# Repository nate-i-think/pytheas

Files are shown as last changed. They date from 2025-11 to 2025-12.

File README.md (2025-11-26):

# about pytheas
Pytheas is a custom ATSAMD21G18A-based (Cortex-M0+, arduino-compatible) flight controller which I have designed for a self-landing, thrust vectoring rocket which is being built by [Princeton Rocketry](https://www.princetonrocketry.com/) at Princeton University. Anyone is welcome to integrate it into their projects as long as they provide appropriate credit. However, no technical support is provided.

# features
 - ATSAMD21G18A microprocessor
   - Programmable via SWD (TagConnect, half-pitch DuPont) and USB
   - 10 exposed GPIO (plus 5 more extras in half-pitch)
   - Exposed I2C (recomended to connect GPS)
   - Everything else you'd expect
 - BMP390 Pressure Sensor
 - LSM6DSOXTR 6-Axis IMU
 - Power Regulation:
   - 5V @ 9A out (buck) with lots of capacitence  
   - 3v3 @ 1A out (LDO)
   - ~6–12V in

# renderings
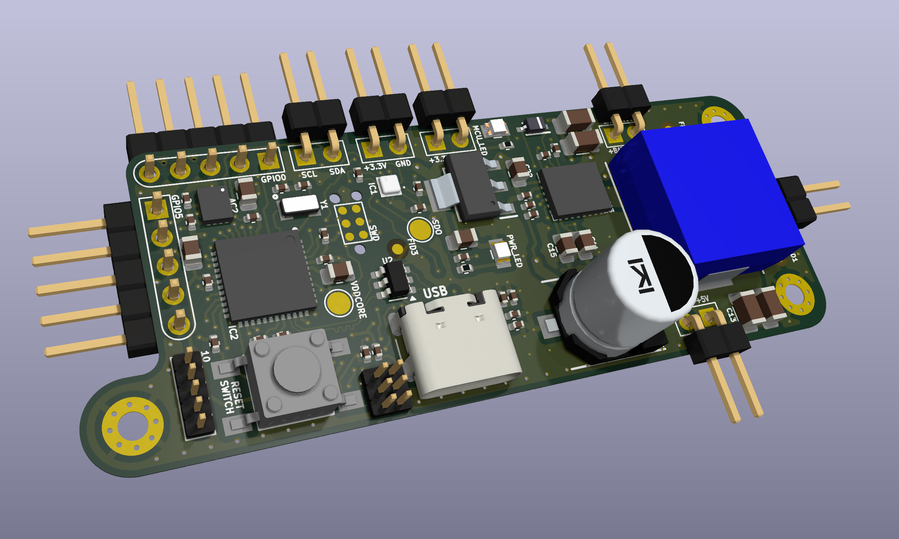
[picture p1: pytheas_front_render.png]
back_render

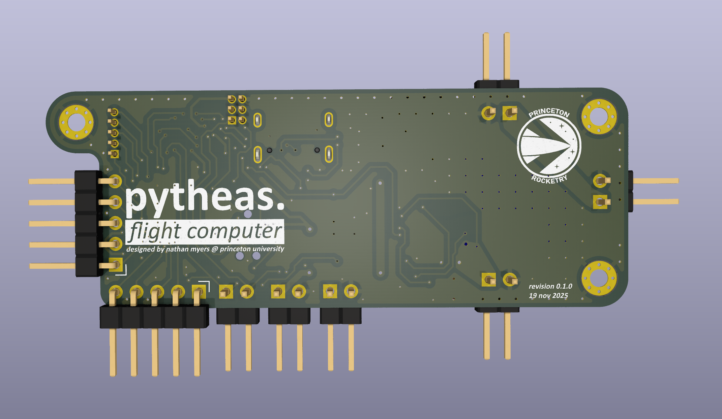
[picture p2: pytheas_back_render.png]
front_render


# layers
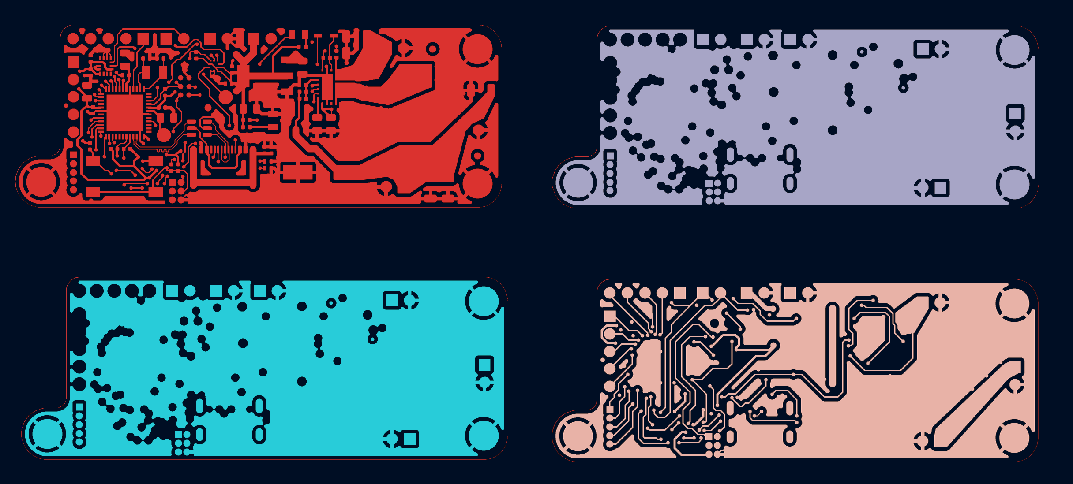
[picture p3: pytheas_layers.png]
layers image


# schematic
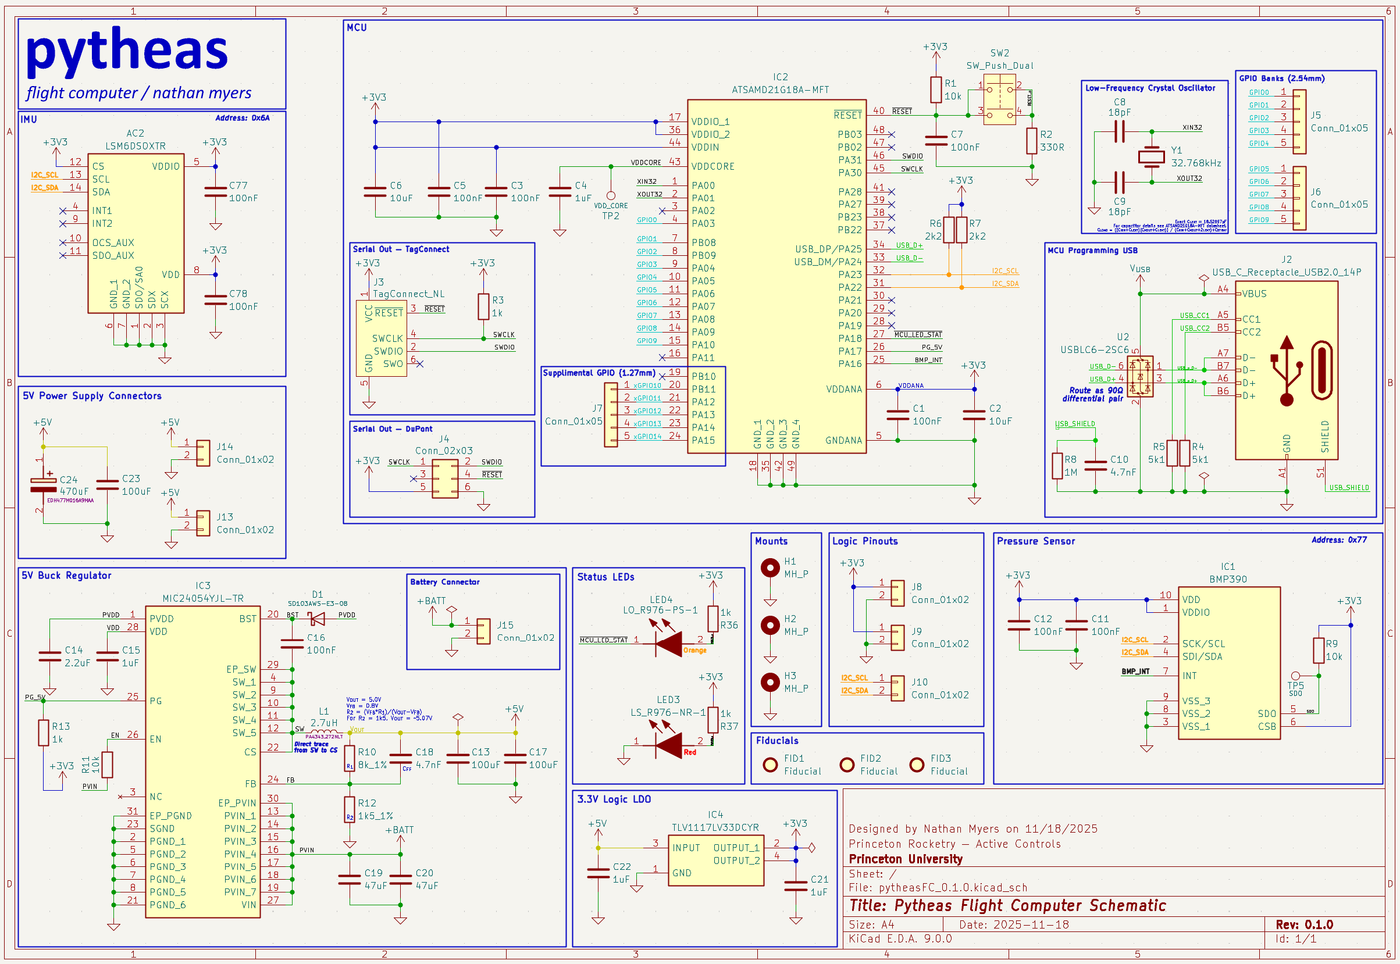
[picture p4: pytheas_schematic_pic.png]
schematic image


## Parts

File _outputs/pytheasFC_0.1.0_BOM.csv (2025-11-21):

Qty | Designator | Value | Footprint | Manufacturer | Manufacturer Part Number
1 | AC2 | LSM6DSOXTR | SamacSys_Parts:LGA-14_1 | STMicroelectronics | LSM6DSOXTR
9 | C1, C3, C5, C7, C11, C12, C16, C77, C78 | 100nF | Capacitor_SMD:C_0402_1005Metric
2 | C2, C6 | 10uF | Capacitor_SMD:C_0805_2012Metric
4 | C4, C15, C21, C22 | 1uF | Capacitor_SMD:C_0805_2012Metric
2 | C8, C9 | 18pF | Capacitor_SMD:C_0402_1005Metric
2 | C10, C18 | 4.7nF | Capacitor_SMD:C_0402_1005Metric
3 | C13, C17, C23 | 100uF | Capacitor_SMD:C_1206_3216Metric
1 | C14 | 2.2uF | Capacitor_SMD:C_0805_2012Metric
2 | C19, C20 | 47uF | Capacitor_SMD:C_1206_3216Metric
1 | C24 | 470uF | SamacSys_Parts:CAPAE830X1050N | KEMET | EDH477M016A9MAA
1 | D1 | SD103AWS-E3-08 | SamacSys_Parts:SOD2713X115N | Vishay Semiconductors | SD103AWS-E3-08
1 | IC1 | BMP390 | SamacSys_Parts:BMP390 | BOSCH | BMP390
1 | IC2 | ATSAMD21G18A-MFT | SamacSys_Parts:QFN50P700X700X90-49N-D | Microchip | ATSAMD21G18A-MFT
1 | IC3 | MIC24054YJL-TR | SamacSys_Parts:MIC24054YJLTR | Microchip | MIC24054YJL-TR
1 | IC4 | TLV1117LV33DCYR | SamacSys_Parts:SOT230P700X180-4N | Texas Instruments | TLV1117LV33DCYR
1 | J2 | USB_C_Receptacle_USB2.0_14P | Connector_USB:USB_C_Receptacle_GCT_USB4105-xx-A_16P_TopMnt_Horizontal | GCT | USB4105-GF-A
1 | L1 | 2.7uH | SamacSys_Parts:INDPM140128X650N | PULSE | PA4343.272NLT
1 | LED3 | LS_R976-NR-1 | SamacSys_Parts:LEDC2012X40N | ams OSRAM | LS R976-NR-1
1 | LED4 | LO_R976-PS-1 | SamacSys_Parts:LEDC2012X90N | ams OSRAM | LO R976-PS-1
3 | R1, R9, R11 | 10k | Capacitor_SMD:C_0402_1005Metric
1 | R2 | 330R | Capacitor_SMD:C_0402_1005Metric
2 | R3, R13 | 1k | Capacitor_SMD:C_0402_1005Metric
2 | R4, R5 | 5k1 | Capacitor_SMD:C_0402_1005Metric
2 | R6, R7 | 2k2 | Capacitor_SMD:C_0402_1005Metric
1 | R8 | 1M | Capacitor_SMD:C_0402_1005Metric
1 | R10 | 8k_1% | Capacitor_SMD:C_0402_1005Metric
1 | R12 | 1k5_1% | Capacitor_SMD:C_0402_1005Metric
2 | R36, R37 | 1k | Resistor_SMD:R_0402_1005Metric
1 | SW2 | SW_Push_Dual | SamacSys_Parts:FSM2J_1 | TE Connectivity / P&B | 2-1437565-8
1 | U2 | USBLC6-2SC6 | Package_TO_SOT_SMD:SOT-23-6 | STMicroelectronics | USBLC6-2SC6
1 | Y1 | 32.768kHz | SamacSys_Parts:ECX-31B | ECS | ECS-.327-12.5-34B-TR

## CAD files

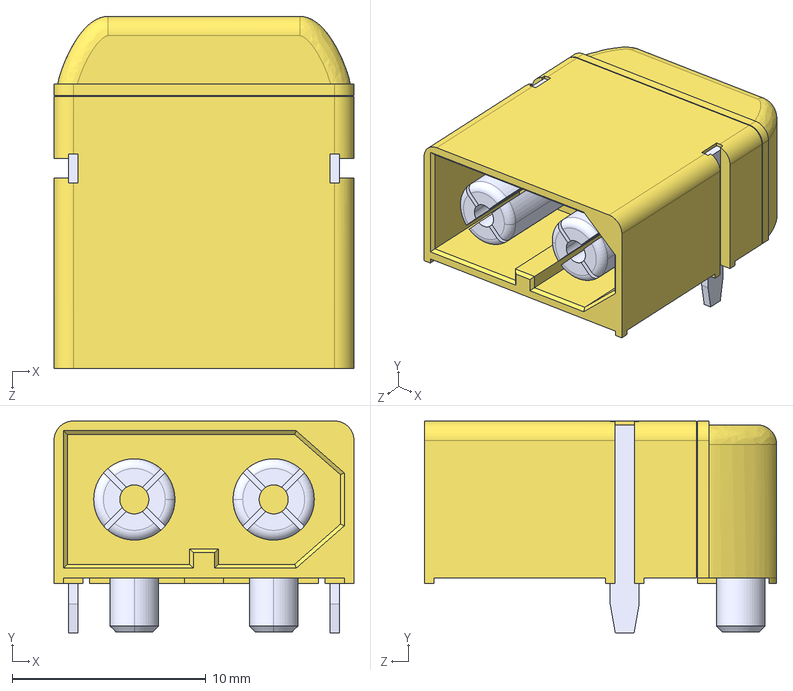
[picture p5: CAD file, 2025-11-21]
Footprints/XT60PW-M/XT60PW-M.step
15.5 x 10.9 x 18.2 mm

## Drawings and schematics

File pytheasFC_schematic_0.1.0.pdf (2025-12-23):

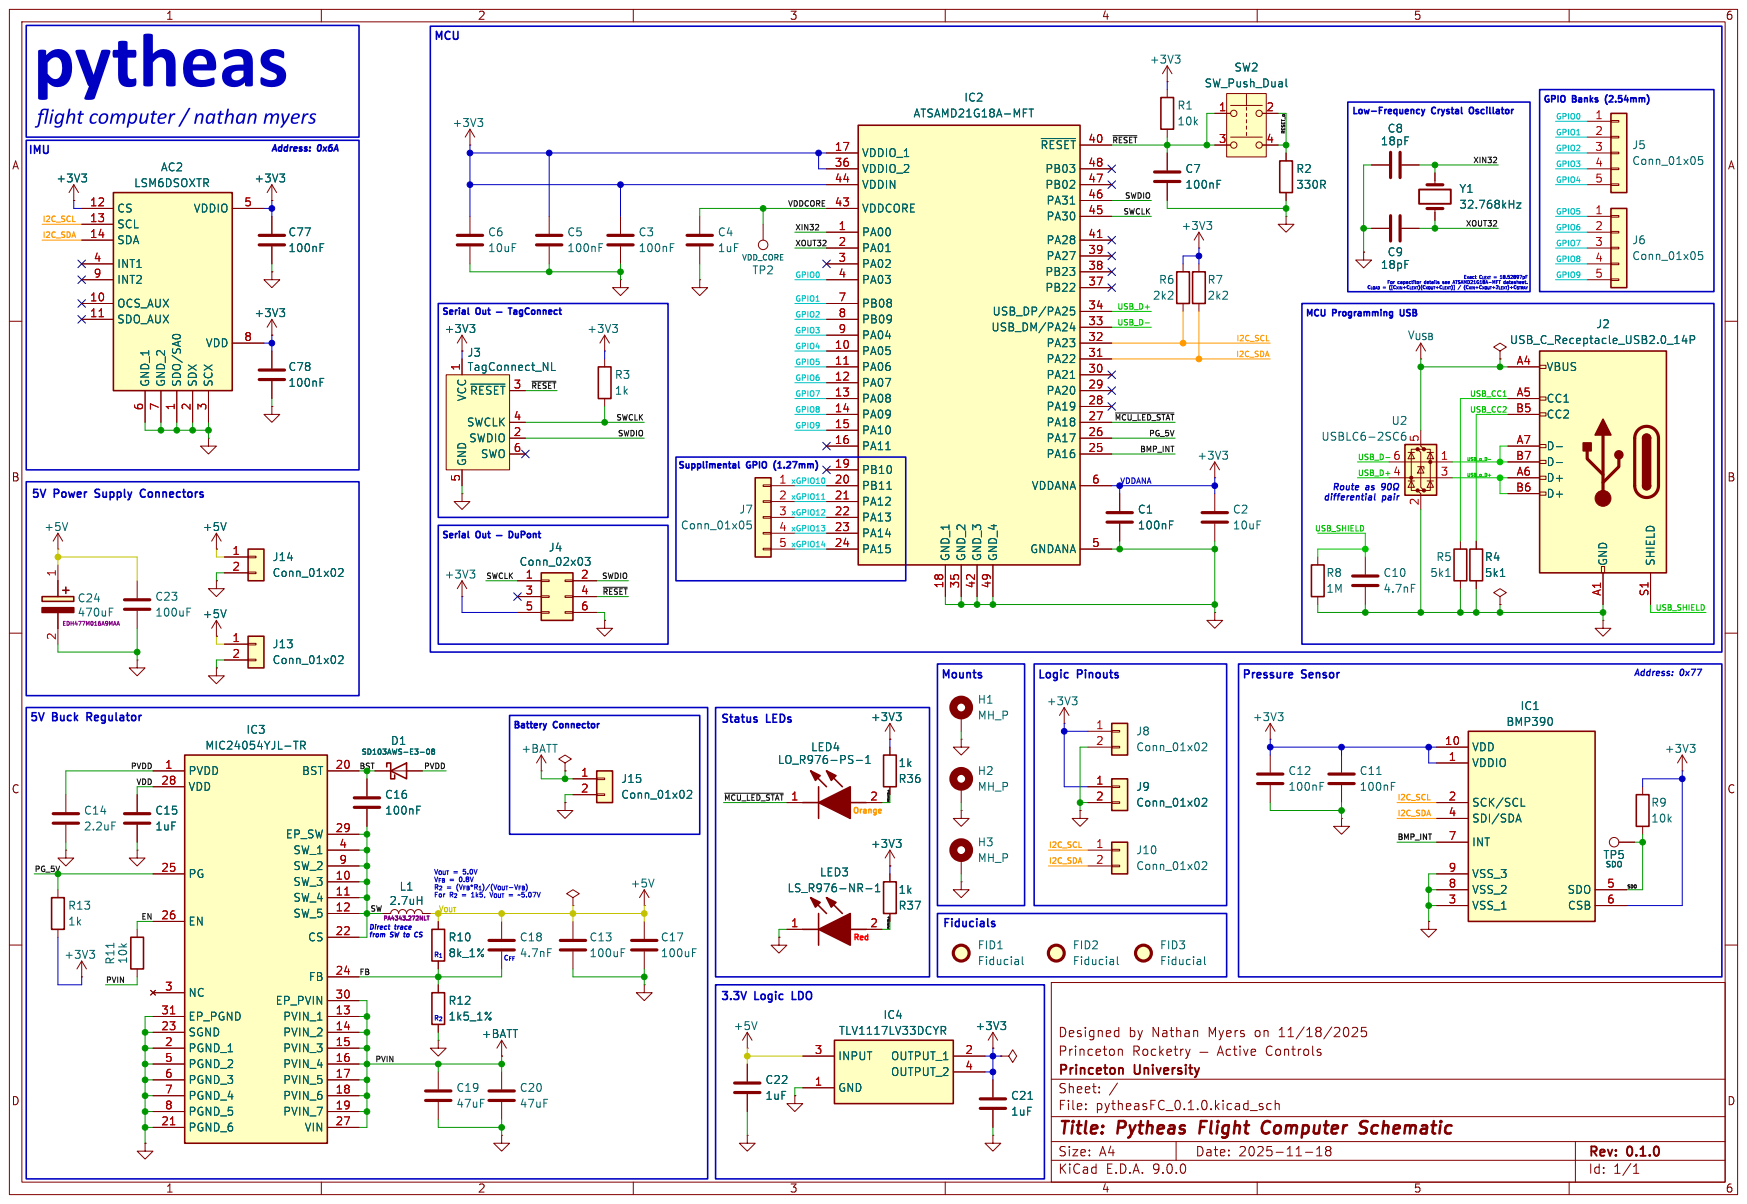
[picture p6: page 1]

5 ~{RESET}3 SWCLK 4 SWDIO 2 SWO 6

Id: 1/1 Title: Pytheas Flight Computer Schematic

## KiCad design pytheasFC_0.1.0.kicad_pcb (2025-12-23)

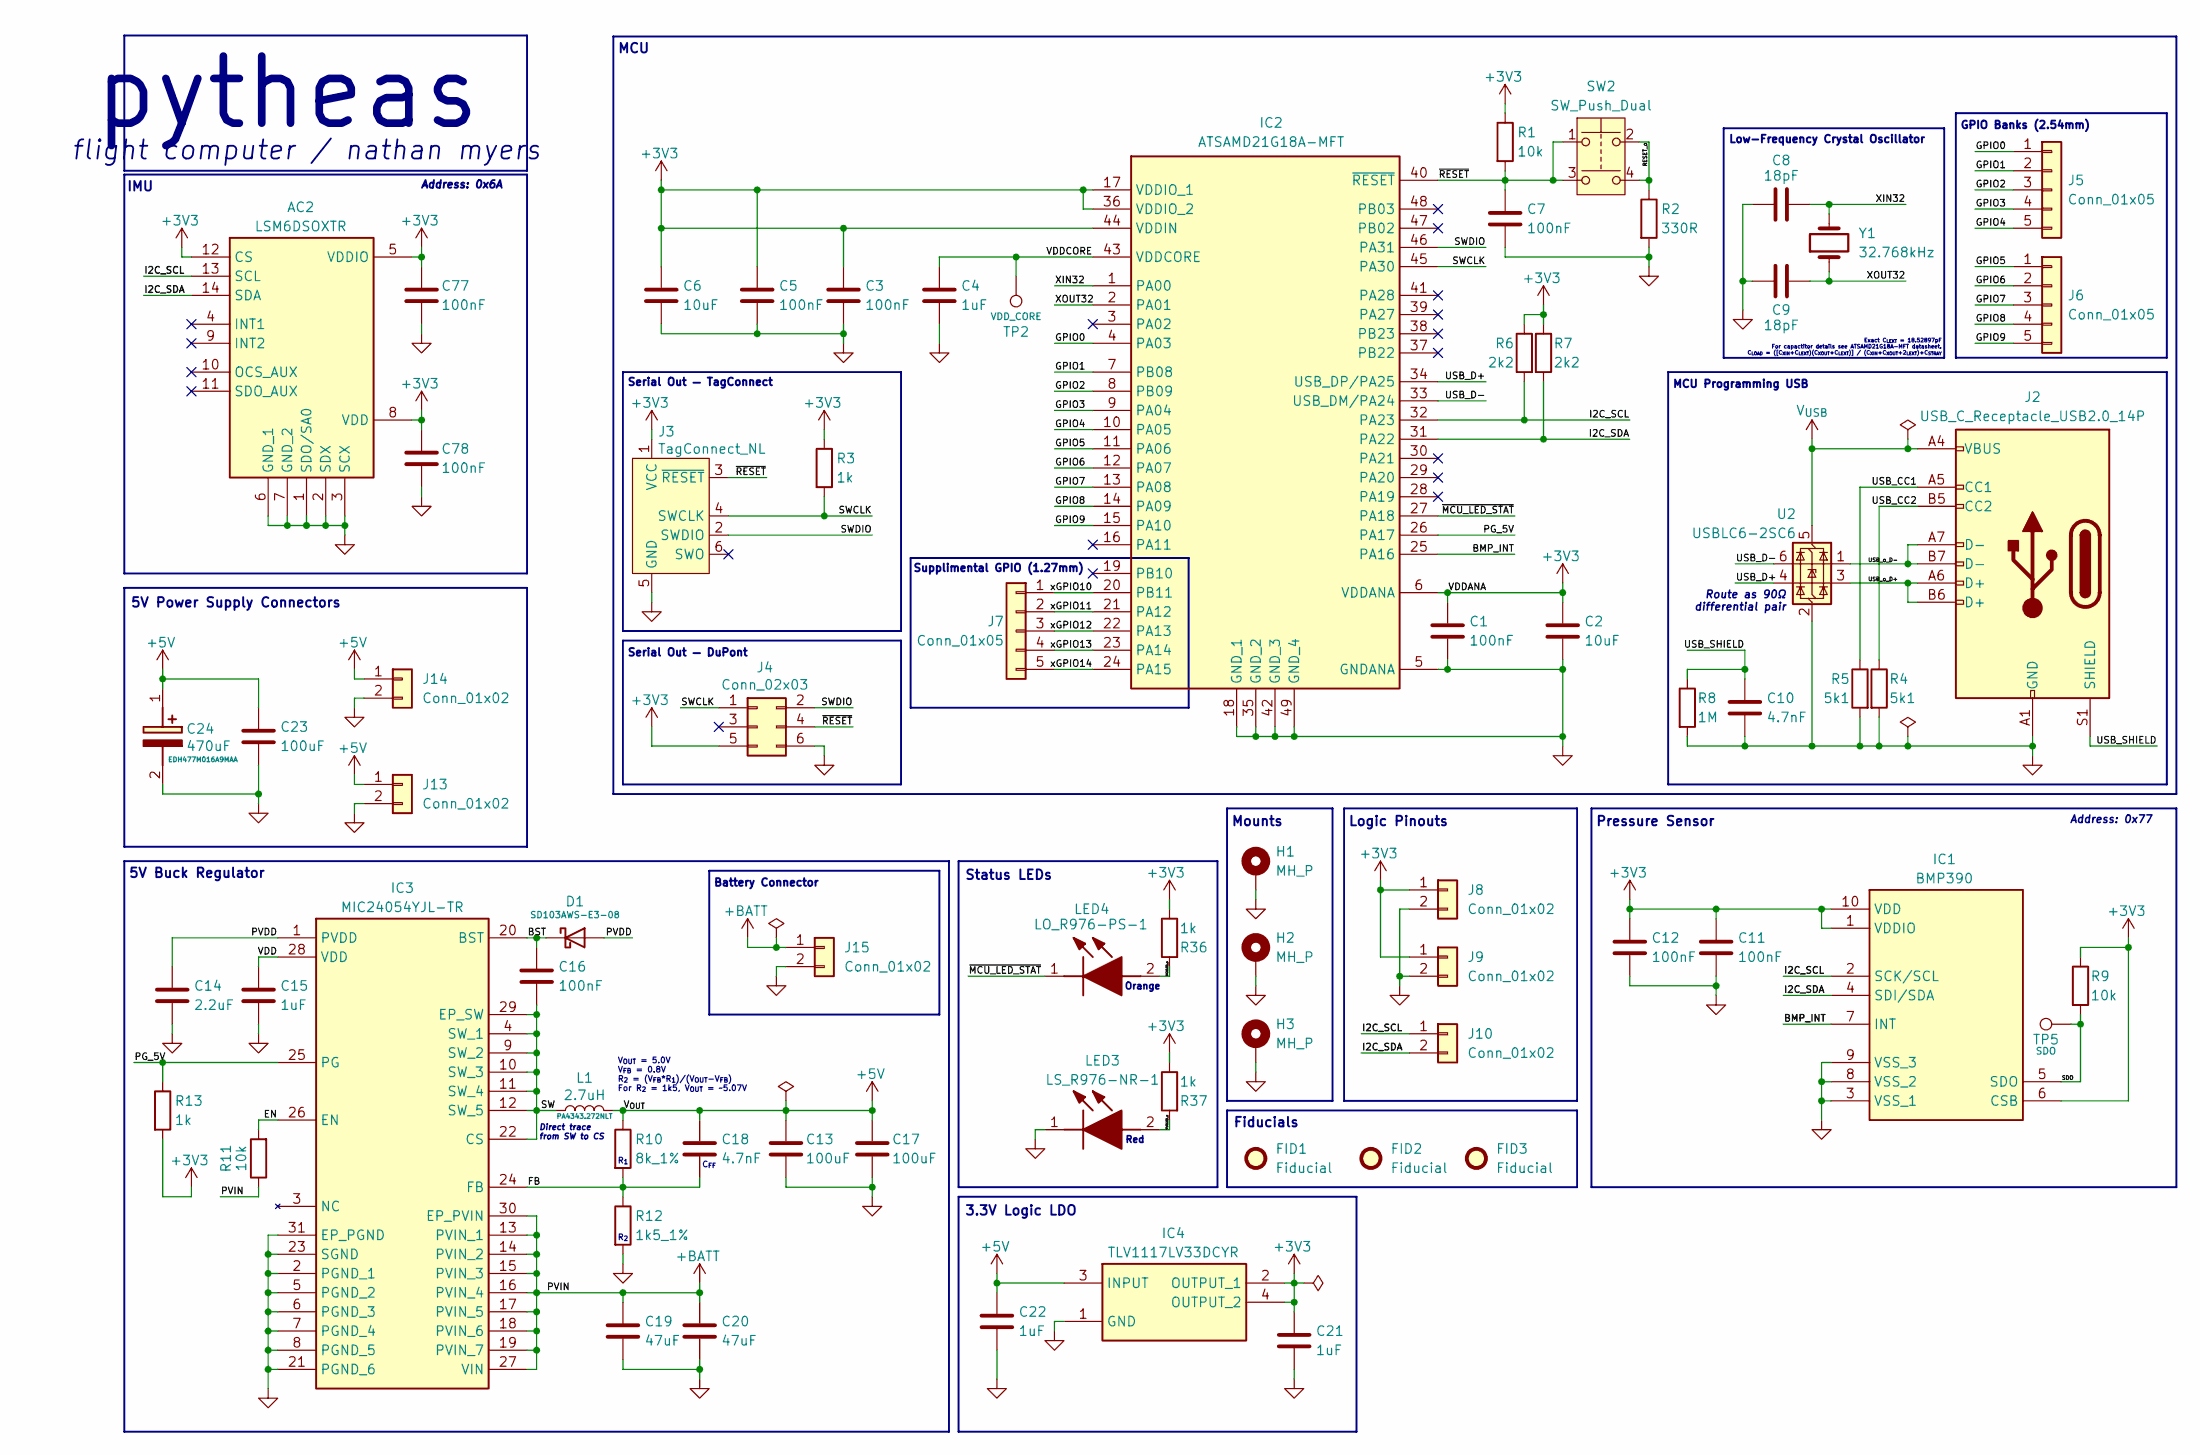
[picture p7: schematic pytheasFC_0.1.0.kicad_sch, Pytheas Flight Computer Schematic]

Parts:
AC2: LSM6DSOXTR; LGA-14_1; Mouser Part Number 511-LSM6DSOXTR
C1, C3, C5, C7, C11, C12, C16, C77, C78: 100nF; C_0402_1005Metric
C2, C6: 10uF; C_0805_2012Metric
C4, C15, C21, C22: 1uF; C_0805_2012Metric
C8, C9: 18pF; C_0402_1005Metric
C10, C18: 4.7nF; C_0402_1005Metric
C13, C17, C23: 100uF; C_1206_3216Metric
C14: 2.2uF; C_0805_2012Metric
C19, C20: 47uF; C_1206_3216Metric
C24: 470uF; CAPAE830X1050N; Mouser Part Number 80-EDH477M016A9MAA
D1: SD103AWS-E3-08; SOD2713X115N; Part Number SD103AWS-E3-08
FID1, FID2, FID3: Fiducial; Fiducial_1mm_Mask2mm
H1, H2, H3: MH_P; MountingHole_2.2mm_M2_Pad_Via
IC1: BMP390; Mouser Part Number 262-BMP390
IC2: ATSAMD21G18A-MFT; QFN50P700X700X90-49N-D; Mouser Part Number 556-ATSAMD21G18A-MFT
IC3: MIC24054YJL-TR; MIC24054YJLTR; Mouser Part Number 998-MIC24054YJLTR
IC4: TLV1117LV33DCYR; SOT230P700X180-4N; Mouser Part Number 595-TLV1117LV33DCYR
J2: USB_C_Receptacle_USB2.0_14P; USB_C_Receptacle_GCT_USB4105-xx-A_16P_TopMnt_Horizontal
J3: TagConnect_NL; Tag-Connect_TC2030-IDC-NL_2x03_P1.27mm_Vertical
J4: Conn_02x03; PinHeader_2x03_P1.27mm_Vertical
J5, J6: Conn_01x05; PinHeader_1x05_P2.54mm_Horizontal
J7: Conn_01x05; PinHeader_1x05_P1.27mm_Vertical
J8, J9, J10, J13, J14, J15: Conn_01x02; PinHeader_1x02_P2.54mm_Horizontal
L1: 2.7uH; INDPM140128X650N; Part Number PA4343.272NLT
LED3: LS_R976-NR-1; LEDC2012X40N; Mouser Part Number 720-LSR976-NR-1
LED4: LO_R976-PS-1; LEDC2012X90N; Mouser Part Number 720-LOR976-PS-1
R1, R9, R11: 10k; R_0402_1005Metric
R2: 330R; R_0402_1005Metric
R3, R13, R36, R37: 1k; R_0402_1005Metric
R4, R5: 5k1; R_0402_1005Metric
R6, R7: 2k2; R_0402_1005Metric
R8: 1M; R_0402_1005Metric
R10: 8k_1%; R_0402_1005Metric
R12: 1k5_1%; R_0402_1005Metric
SW2: SW_Push_Dual; FSM2J_1; Part Number 2-1437565-8
TP2: VDD_CORE; TestPoint_Pad_D2.0mm
TP5: SDO; TestPoint_Pad_D2.0mm
U2: USBLC6-2SC6; SOT-23-6
Y1: 32.768kHz; ECX-31B; Part Number ECS-.327-12.5-34B-TR

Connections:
+3V3: AC2.5 (VDDIO), AC2.8 (VDD), AC2.12 (CS), C1.1, C2.1, C3.1, C5.1, C6.1, C11.1, C12.1, C21.1, C77.1, C78.1, IC1.1 (VDDIO), IC1.6 (CSB), IC1.10 (VDD), IC2.6 (VDDANA), IC2.17 (VDDIO_1), IC2.36 (VDDIO_2), IC2.44 (VDDIN), IC4.2 (OUTPUT_1), IC4.4 (OUTPUT_2), J3.1 (VCC), J4.5, J8.1, J9.1, R1.1, R3.1, R6.1, R7.1, R9.1, R13.2, R36.1, R37.1
+5V: C13.1, C17.1, C18.1, C22.1, C23.1, C24.1 (+), IC4.3 (INPUT), J13.1, J14.1, L1.2, R10.1
+BATT: C19.1, C20.1, IC3.13 (PVIN_1), IC3.14 (PVIN_2), IC3.15 (PVIN_3), IC3.16 (PVIN_4), IC3.17 (PVIN_5), IC3.18 (PVIN_6), IC3.19 (PVIN_7), IC3.27 (VIN), IC3.30 (EP_PVIN), J15.1, R11.1
/BMP_INT: IC1.7 (INT), IC2.25 (PA16)
/BST: C16.1, D1.1 (K), IC3.20 (BST)
/EN: IC3.26 (EN), R11.2
/FB: C18.2, IC3.24 (FB), R10.2, R12.1
/GPIO0: IC2.4 (PA03), J5.1
/GPIO1: IC2.7 (PB08), J5.2
/GPIO2: IC2.8 (PB09), J5.3
/GPIO3: IC2.9 (PA04), J5.4
/GPIO4: IC2.10 (PA05), J5.5
/GPIO5: IC2.11 (PA06), J6.1
/GPIO6: IC2.12 (PA07), J6.2
/GPIO7: IC2.13 (PA08), J6.3
/GPIO8: IC2.14 (PA09), J6.4
/GPIO9: IC2.15 (PA10), J6.5
/I2C_SCL: AC2.13 (SCL), IC1.2 (SCK/SCL), IC2.32 (PA23), J10.1, R6.2
/I2C_SDA: AC2.14 (SDA), IC1.4 (SDI/SDA), IC2.31 (PA22), J10.2, R7.2
/MCULED_o: LED4.2 (A), R36.2
/PG_5V: IC2.26 (PA17), IC3.25 (PG), R13.1
/PVDD: C14.1, D1.2 (A), IC3.1 (PVDD)
/PWRLED_o: LED3.2 (A), R37.2
/RESET_o: R2.1, SW2.2, SW2.4
/SDO: IC1.5 (SDO), R9.2, TP5.1
/SW: C16.2, IC3.4 (SW_1), IC3.9 (SW_2), IC3.10 (SW_3), IC3.11 (SW_4), IC3.12 (SW_5), IC3.22 (CS), IC3.29 (EP_SW), L1.1
/SWCLK: IC2.45 (PA30), J3.4 (SWCLK), J4.1, R3.2
/SWDIO: IC2.46 (PA31), J3.2 (SWDIO), J4.2
/USB_CC1: J2.A5 (CC1), R5.1
/USB_CC2: J2.B5 (CC2), R4.1
/USB_D+: IC2.34 (USB_DP/PA25), U2.4 (I/O2)
/USB_D-: IC2.33 (USB_DM/PA24), U2.6 (I/O1)
/USB_SHIELD: C10.1, J2.S1 (SHIELD), R8.1
/USB_o_D+: J2.A6 (D+), J2.B6 (D+), U2.3 (I/O2)
/USB_o_D-: J2.A7 (D-), J2.B7 (D-), U2.1 (I/O1)
/VDD: C15.1, IC3.28 (VDD)
/VDDCORE: C4.1, IC2.43 (VDDCORE), TP2.1
/XIN32: C8.2, IC2.1 (PA00), Y1.2
/XOUT32: C9.1, IC2.2 (PA01), Y1.1
/xGPIO10: IC2.20 (PB11), J7.1
/xGPIO11: IC2.21 (PA12), J7.2
/xGPIO12: IC2.22 (PA13), J7.3
/xGPIO13: IC2.23 (PA14), J7.4
/xGPIO14: IC2.24 (PA15), J7.5
/~MCU_LED_STAT: IC2.27 (PA18), LED4.1 (K)
/~RESET: C7.1, IC2.40 (~RESET), J3.3 (~RESET), J4.4, R1.2, SW2.1, SW2.3
GND: AC2.1 (SDO/SA0), AC2.2 (SDX), AC2.3 (SCX), AC2.6 (GND_1), AC2.7 (GND_2), C1.2, C2.2, C3.2, C4.2, C5.2, C6.2, C7.2, C8.1, C9.2, C10.2, C11.2, C12.2, C13.2, C14.2, C15.2, C17.2, C19.2, C20.2, C21.2, C22.2, C23.2, C24.2 (-), C77.2, C78.2, H1.1, H2.1, H3.1, IC1.3 (VSS_1), IC1.8 (VSS_2), IC1.9 (VSS_3), IC2.5 (GNDANA), IC2.18 (GND_1), IC2.35 (GND_2), IC2.42 (GND_3), IC2.49 (GND_4), IC3.2 (PGND_1), IC3.5 (PGND_2), IC3.6 (PGND_3), IC3.7 (PGND_4), IC3.8 (PGND_5), IC3.21 (PGND_6), IC3.23 (SGND), IC3.31 (EP_PGND), IC4.1 (GND), J2.A1 (GND), J2.A12 (GND), J2.B1 (GND), J2.B12 (GND), J3.5 (GND), J4.6, J8.2, J9.2, J13.2, J14.2, J15.2, LED3.1 (K), R2.2, R4.2, R5.2, R8.2, R12.2, U2.2 (GND)
V_{USB}: J2.A4 (VBUS), J2.A9 (VBUS), J2.B4 (VBUS), J2.B9 (VBUS), U2.5 (VBUS)

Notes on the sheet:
Address: 0x6A
Pressure Sensor
Low-Frequency Crystal Oscillator
5V Buck Regulator
5V Power Supply Connectors
Serial Out — TagConnect
Logic Pinouts
Route as 90Ω differential pair
Fiducials
Address: 0x77
R_{1}
IMU
MCU
Orange
Direct trace from SW to CS
Mounts
Serial Out — DuPont
R_{2}
Battery Connector
C_{FF}
V_{OUT} = 5.0V V_{FB} = 0.8V R_{2} = (V_{FB}*R_{1})/(V_{OUT}-V_{FB}) For R_{2} = 1k5, V_{OUT} = ~5.07V
flight computer / nathan myers
GPIO Banks (2.54mm)
Exact C_{LEXT} = 18.52897pF For capactitor details see ATSAMD21G18A-MFT datasheet. C_{LOAD} = ([C_{XIN}+C_{LEXT})(C_{XOUT}+C_{LEXT})] / (C_{XIN}+C_{XOUT}+2_{LEXT})+C_{STRAY}
Status LEDs
Supplimental GPIO (1.27mm)
MCU Programming USB
3.3V Logic LDO
Red
pytheas

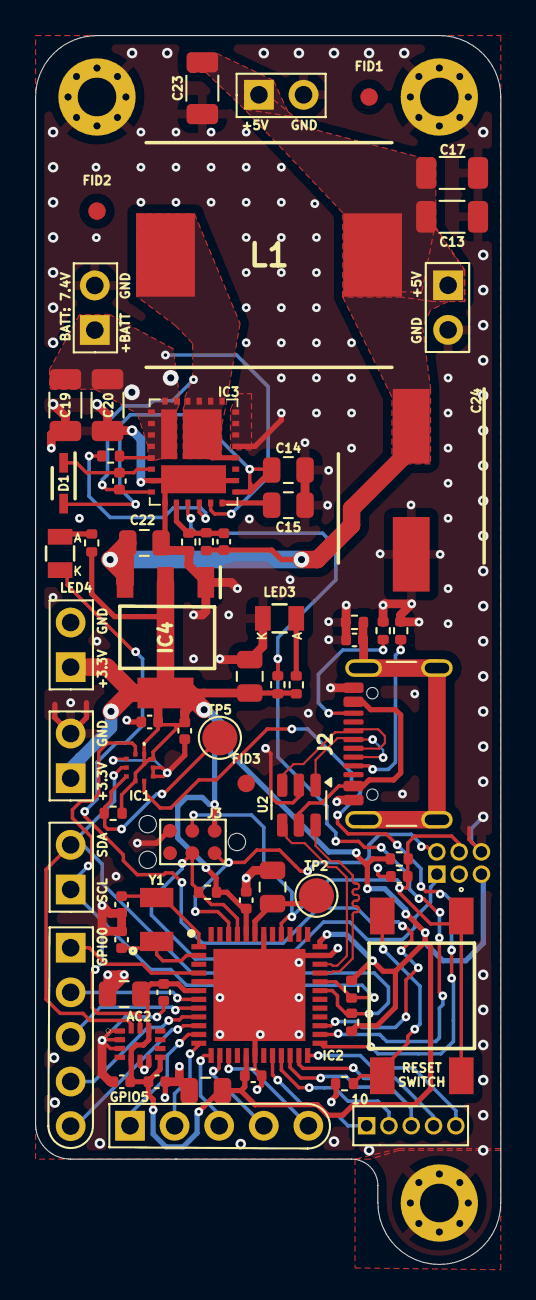
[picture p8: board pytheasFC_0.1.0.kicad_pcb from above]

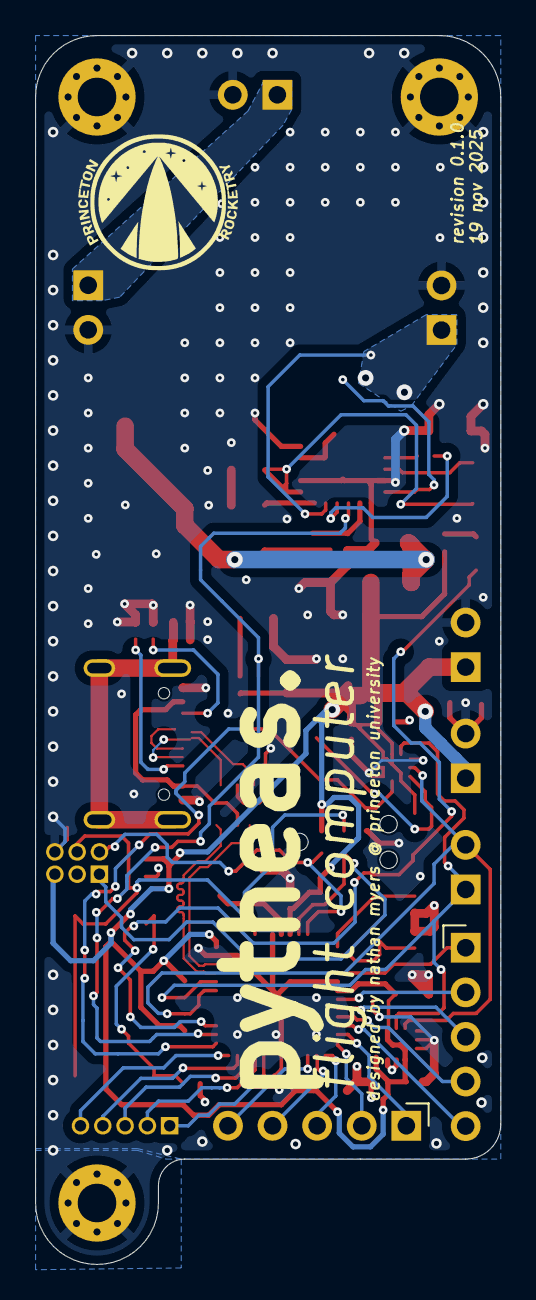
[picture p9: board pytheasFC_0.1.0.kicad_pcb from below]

Board: 4 copper layers, 26.5 x 70.0 mm, 73 parts (2 on the bottom side), 48 nets.

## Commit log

2025-11-21 initial commit, pytheas 0.1.0
    [XT60PW-M.step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]
2025-11-21 add schematic
2025-11-27 Update Mounting Hole Positions
    [pytheasFC_0.1-B_Cu.gbr, pytheasFC_0.1-B_Mask.gbr, pytheasFC_0.1-B_Paste.gbr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]
2025-12-23 update VDDANA net and connections
    [pytheasFC_0.1-B_Cu.gbr, pytheasFC_0.1-B_Mask.gbr, pytheasFC_0.1-B_Paste.gbr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]
2025-12-27 modify CPL
    [pytheasFC_0.1.0-all-pos.csv]
2025-12-27 modify CPL againnn
    [pytheasFC_0.1.0-all-pos.csv]
